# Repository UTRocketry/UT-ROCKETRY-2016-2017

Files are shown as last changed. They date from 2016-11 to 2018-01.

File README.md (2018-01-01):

# UT Rocketry Active Control Unit #
## About ##
The Active Roll Control Unit (ARCU) is an electronics platform specially designed for the 2016-2017 NASA
University Student Launch Initiative (NASA USLI) by the University of Toledo Rocketry Club.

The ARCU accomplishes the task of controlling the roll orientation of a high powered rocket (HPR) after 
motor burnout. For the 2016-2017 USLI, NASA sets the requirement that the HPR must complete 2 rolls either
CW or CCW post motor burnout and hold the final roll orientation for the remainder of the flight. This is 
accomplished through the use of a servo motor that will control the angle of fins. The ARCU is composed of 
numerous components but most notably: ATmega32u4 microcontroller (MCU) now using the ESP8266 12E module, 
MPU9250 inertial measurement unit (IMU), and a micro SD card.

The ARCU is Arduino compatable and initially used the Sparkfun Pro Micro 3.3V 8MHz bootloader. Currently the 
system uses the ESP8266 ESP12E module. The MPU9250 is a magnetometer, accelerometer, and gyroscope chip that 
will be used for position feedback in the control loop. The library for the MPU9250 is available from Sparkfun. 
Gyro and Accelerometer data is used during the flight of the rocket to control the rocket. All data from the IMU
is logged during flight and magnetometer data is analyzed post flight to verify the roll of the rocket.

The final form of the ARCU is implemented as a custom printed circuit board (PCB). However since the ARCU 
uses parts available from Sparkfun, the ARCU can be assembled easily from off the shelf components either 
on a breadboard or using protyping board.Released versions of the ARCU PCB, ARCU ICSP tool, and the Backup
Breakout version are available in the "RELEASE" sub folder.

The University of Toledo Rocketry Club learned most of the information appparent in the design and construction 
of the ARCU through the internet. If it wasn't for websites like Adafruit or Sparkfun, the ARCU project would 
not be able to be completed. Knowing this, the University of Toledo Rocketry Club has made all designs of the 
ARCU available online for public access so that others can learn from the project. The ARCU is licensed under 
the GPL 3.0 license and is Open Source Hardware and Software.

## Revision History ##
### ATMega32U4 REV A ###
- This version had issues with USB connectivity and flashing the bootloader

### ATMega32U4 REV B ###
- This version attempted fix issues with the USB in the previous version, however the fixes were unsuccessful
- THe issues may have been due to the flashing tool that was used for the bootloader

### ESP8266 REV A ###
- This board was mostly functional with the exception of the interrupt pin on the 4 pin header being non-functional

### ICSP Tool ###

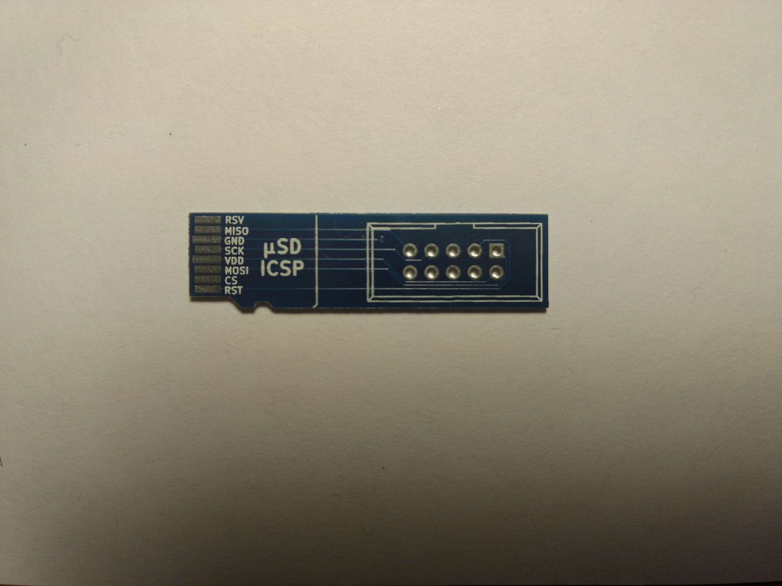
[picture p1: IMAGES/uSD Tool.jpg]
image goes here


- This was designed to flash the bootloader on the boards running the ATMega32U4. Pinouts for the ICSP header are wrong and backwards
- This tool is printed at the same thickness as a standard micro SD card and is designed to fit into a micro SD card slot.

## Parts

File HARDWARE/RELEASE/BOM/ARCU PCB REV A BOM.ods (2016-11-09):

Quantity | Reference | Value | Package | Part Number
ARCU PCB
3 | R1, R4, R5 | 10K, 5%, 1/8W | 0805 | RMCF0805JT10K0
2 | R2, R3 | 22, 5%, 1/8W | 0805 | RMCF0805JT22R0
2 | C1, C2 | 22pF, 1%, 10V | 0805 | CL21C220FBANNNC
1 | C3 | 1uF, 10%, 10V | 0805 | CL21B105KAFNNNE
3 | C4, C7, C8 | .1uF, 10%, 10V | 0805 | CL21B104KBCNNNC
1 | C5 | 10uF, 10%, 10V | 0805 | CL21A106KPFNNNE
1 | C6 | 22uF, 10%, 10V | 0805 | CL21A226MQCLQNC
1 | D1 | Schottky Diode, 1A | SOD-323 | BAT760-7
1 | D2 | Blue LED, | 0805 | LTST-C171TBKT
1 | F1 | Fuse, Poly, 500mA Hold, 1000mA Trip | 1210 | 0ZCH0050FF2G
1 | P1 | Female 1x3 Locking Polarized Conn. | CUSTOM | 5-103635-2
1 |  | Male Mating Conn. For P1 | NONE | 104257-2
3 |  | Pins for P1 Conn. | NONE | 104479-8
1 | P2 | MICRO SD, Push Push | CUSTOM | DM3CS-SF
1 | U1 | ATmega32U4, RC Clock | TQFP-44 10x10mm 0.8mm Pitch | ATMEGA32U4RC-AUR
1 | U2 | AZ1117, 3.3V Fixed Regulator | SOT-223 | AZ1117CH-3.3TRG1
1 | U3 | MPU-9250, 9 Axis IMU, I2C | QFN-40 3mmX3mm Pitch .4mm | MPU-9250
1 | U4 | ESP-01v090, Serial Wifi Module | CUSTOM | WRL-13678
1 | X1 | SMD USB OTG, Female Mini USB | CUSTOM | UX60-MB-5ST
1 | Y1 | Crystal, 8MHz | CUSTOM | ABM3-8.000MHZ-D2Y-T
University of Toledo Rocketry Club
 |  | Active Roll Control Unit (ARCU) | Rev. A 11/3/2016
Quantity | Reference | Value | Package | Part Number
ARCU ICSP
1 | P1 | 2x5 IDC Conn. | 2X5 ICSP Conn., .1” Pitch PTH | 3020-10-0100-00
Battery and Servo Wiring
1 | NONE | XT60 Conn. Male and Female Pair | NONE | PRT-10474
1 | NONE | 9V Battery Snap | NONE | Keystone 84-4
Backup Breakout Version
1 | P1 | 1X3. 1” Pitch Male Header PTH | NONE | PRT-00553
1 | U1 | Sparkfun Pro Micro 3.3V 8MHz | NONE | DEV-12587
1 | U2 | Sparkfun MPU9250 | NONE | SEN-13762
1 | U3 | Sparkfun Transflash | NONE | BOB-00544
1 | NONE | XT60 Male and Female Pair | NONE | PRT-10474
1 | NONE | 9V Battery Snap | NONE | PRT-00091
University of Toledo Rocketry Club
 |  | Active Roll Control Unit (ARCU) | Rev. A 11/3/2016

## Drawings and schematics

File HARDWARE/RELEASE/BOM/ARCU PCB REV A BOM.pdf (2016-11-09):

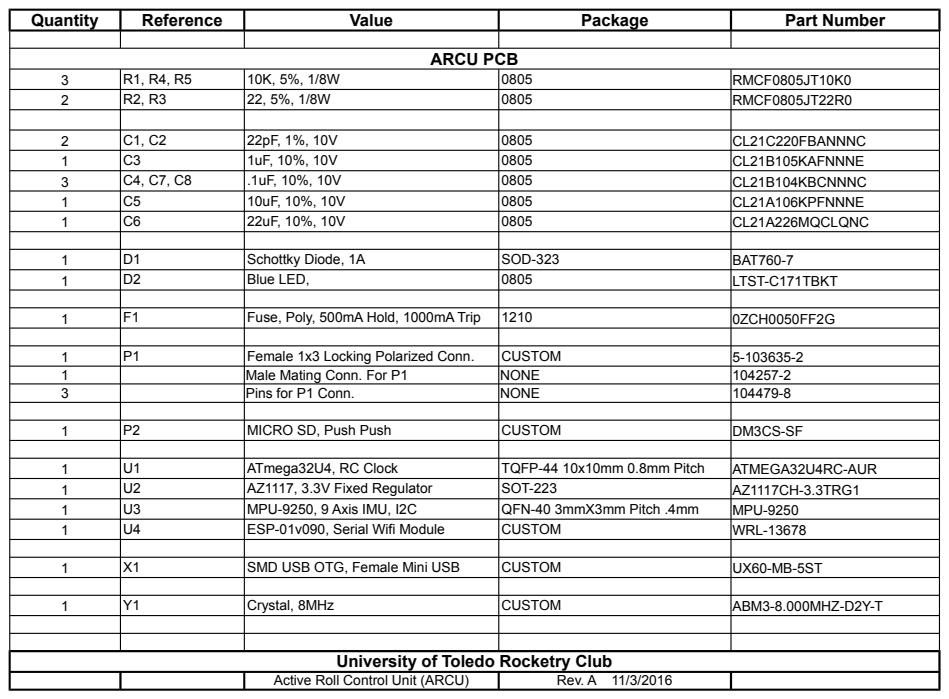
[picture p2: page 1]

University of Toledo Rocketry Club

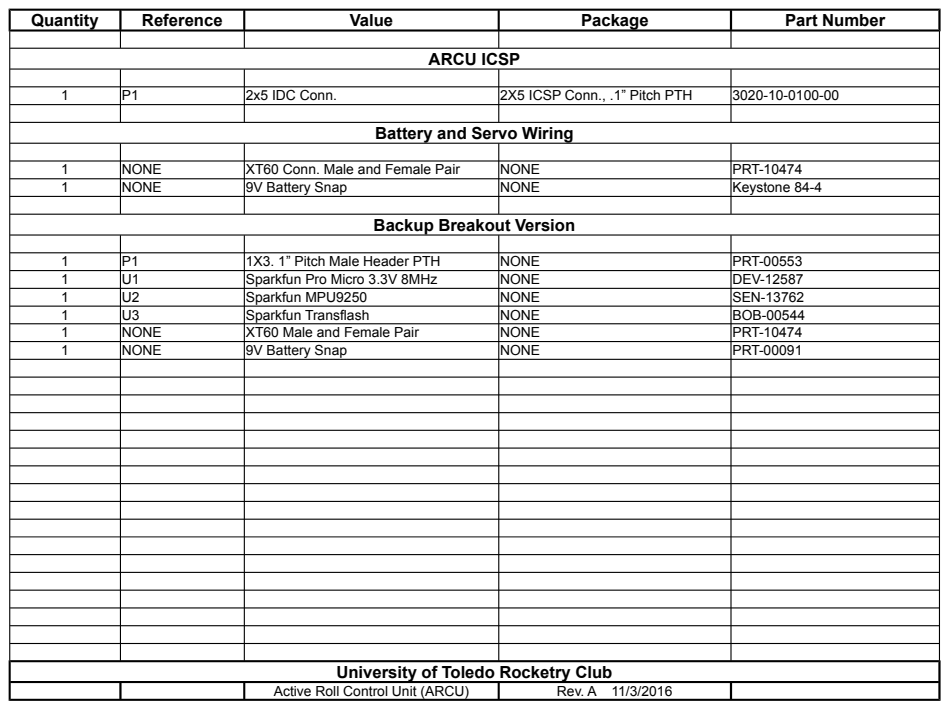
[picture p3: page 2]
Quantity; Reference; Value; Package; Part Number; ARCU ICSP; 2x5 IDC Conn.; 2X5 ICSP Conn., .1” Pitch PTH; NONE; XT60 Conn. Male and Female Pair; PRT-10474; 9V Battery Snap; Keystone 84-4; 1X3. 1” Pitch Male Header PTH; PRT-00553; Sparkfun Pro Micro 3.3V 8MHz; DEV-12587; Sparkfun MPU9250; SEN-13762; Sparkfun Transflash; BOB-00544; XT60 Male and Female Pair; PRT-00091; Active Roll Control Unit (ARCU); Rev. A 11/3/2016

Battery and Servo Wiring

Backup Breakout Version

University of Toledo Rocketry Club

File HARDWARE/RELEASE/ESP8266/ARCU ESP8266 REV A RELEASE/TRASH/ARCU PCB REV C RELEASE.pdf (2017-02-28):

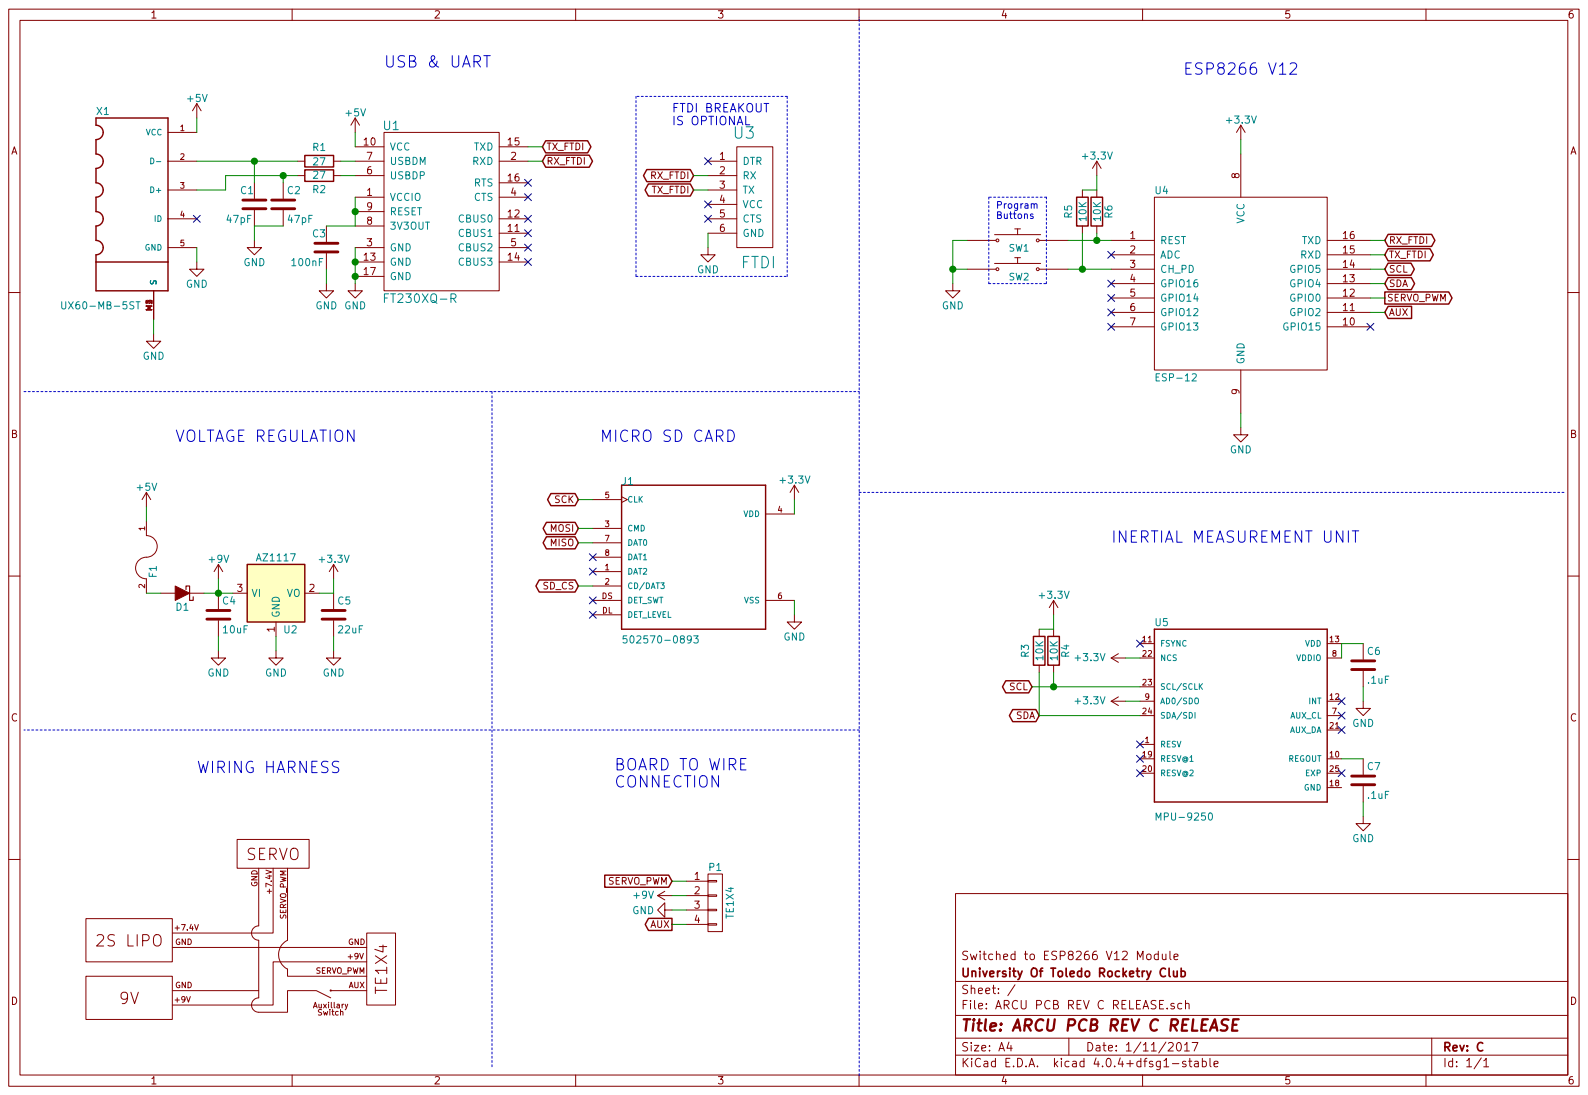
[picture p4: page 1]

+3.3V GND MICRO SD CARD

File: ARCU PCB REV C RELEASE.sch Sheet: / University Of Toledo Rocketry Club Switched to ESP8266 V12 Module

Id: 1/1 Title: ARCU PCB REV C RELEASE

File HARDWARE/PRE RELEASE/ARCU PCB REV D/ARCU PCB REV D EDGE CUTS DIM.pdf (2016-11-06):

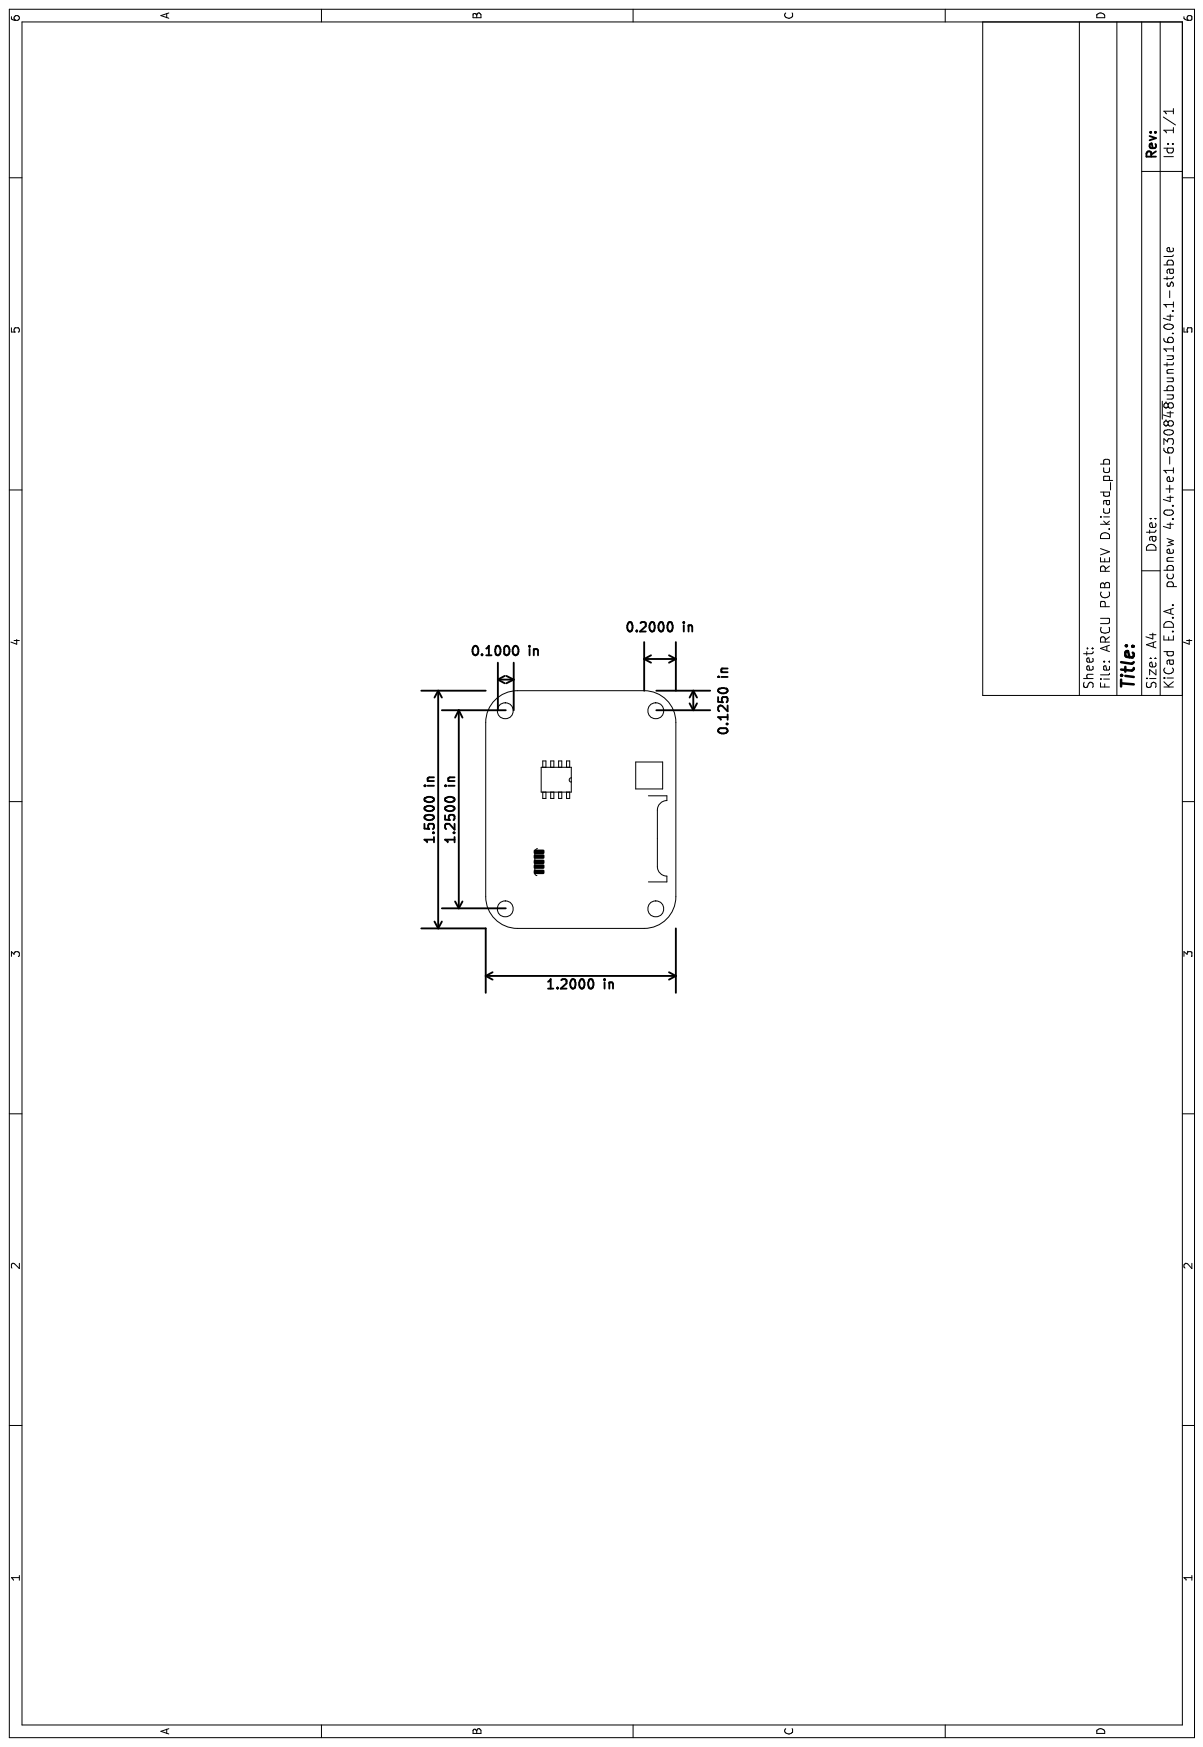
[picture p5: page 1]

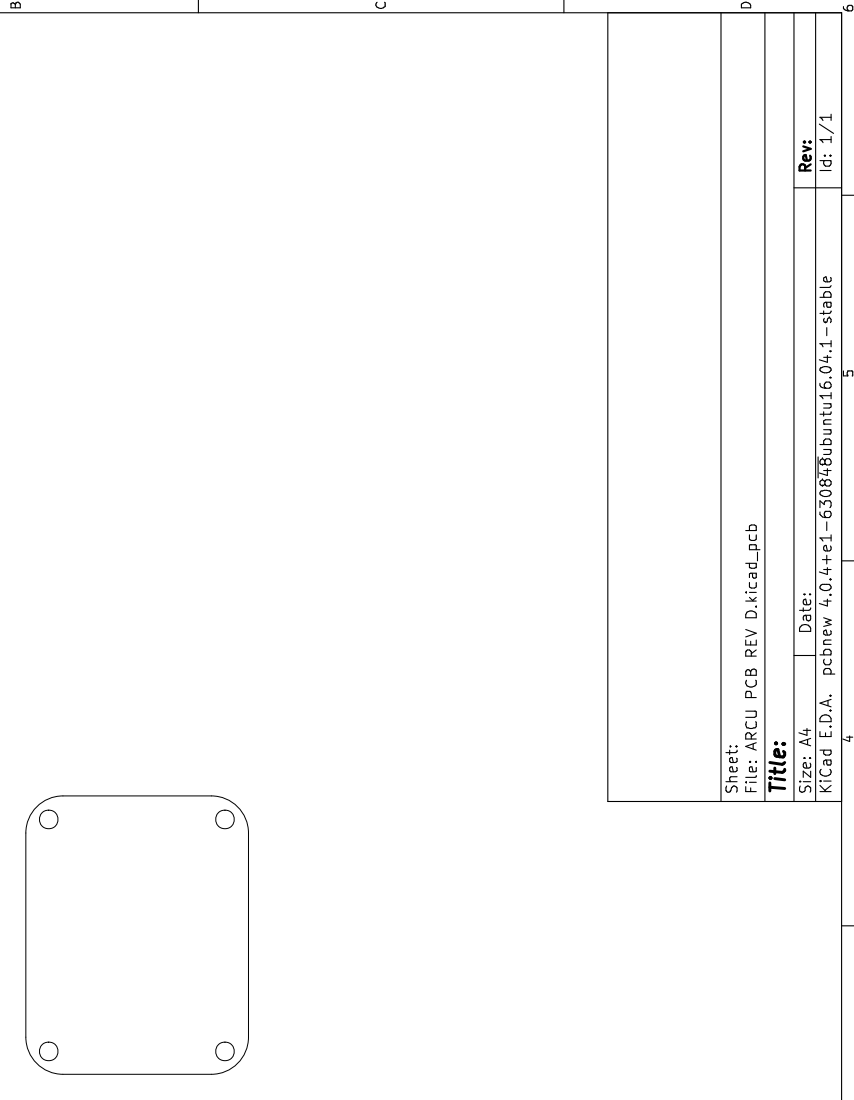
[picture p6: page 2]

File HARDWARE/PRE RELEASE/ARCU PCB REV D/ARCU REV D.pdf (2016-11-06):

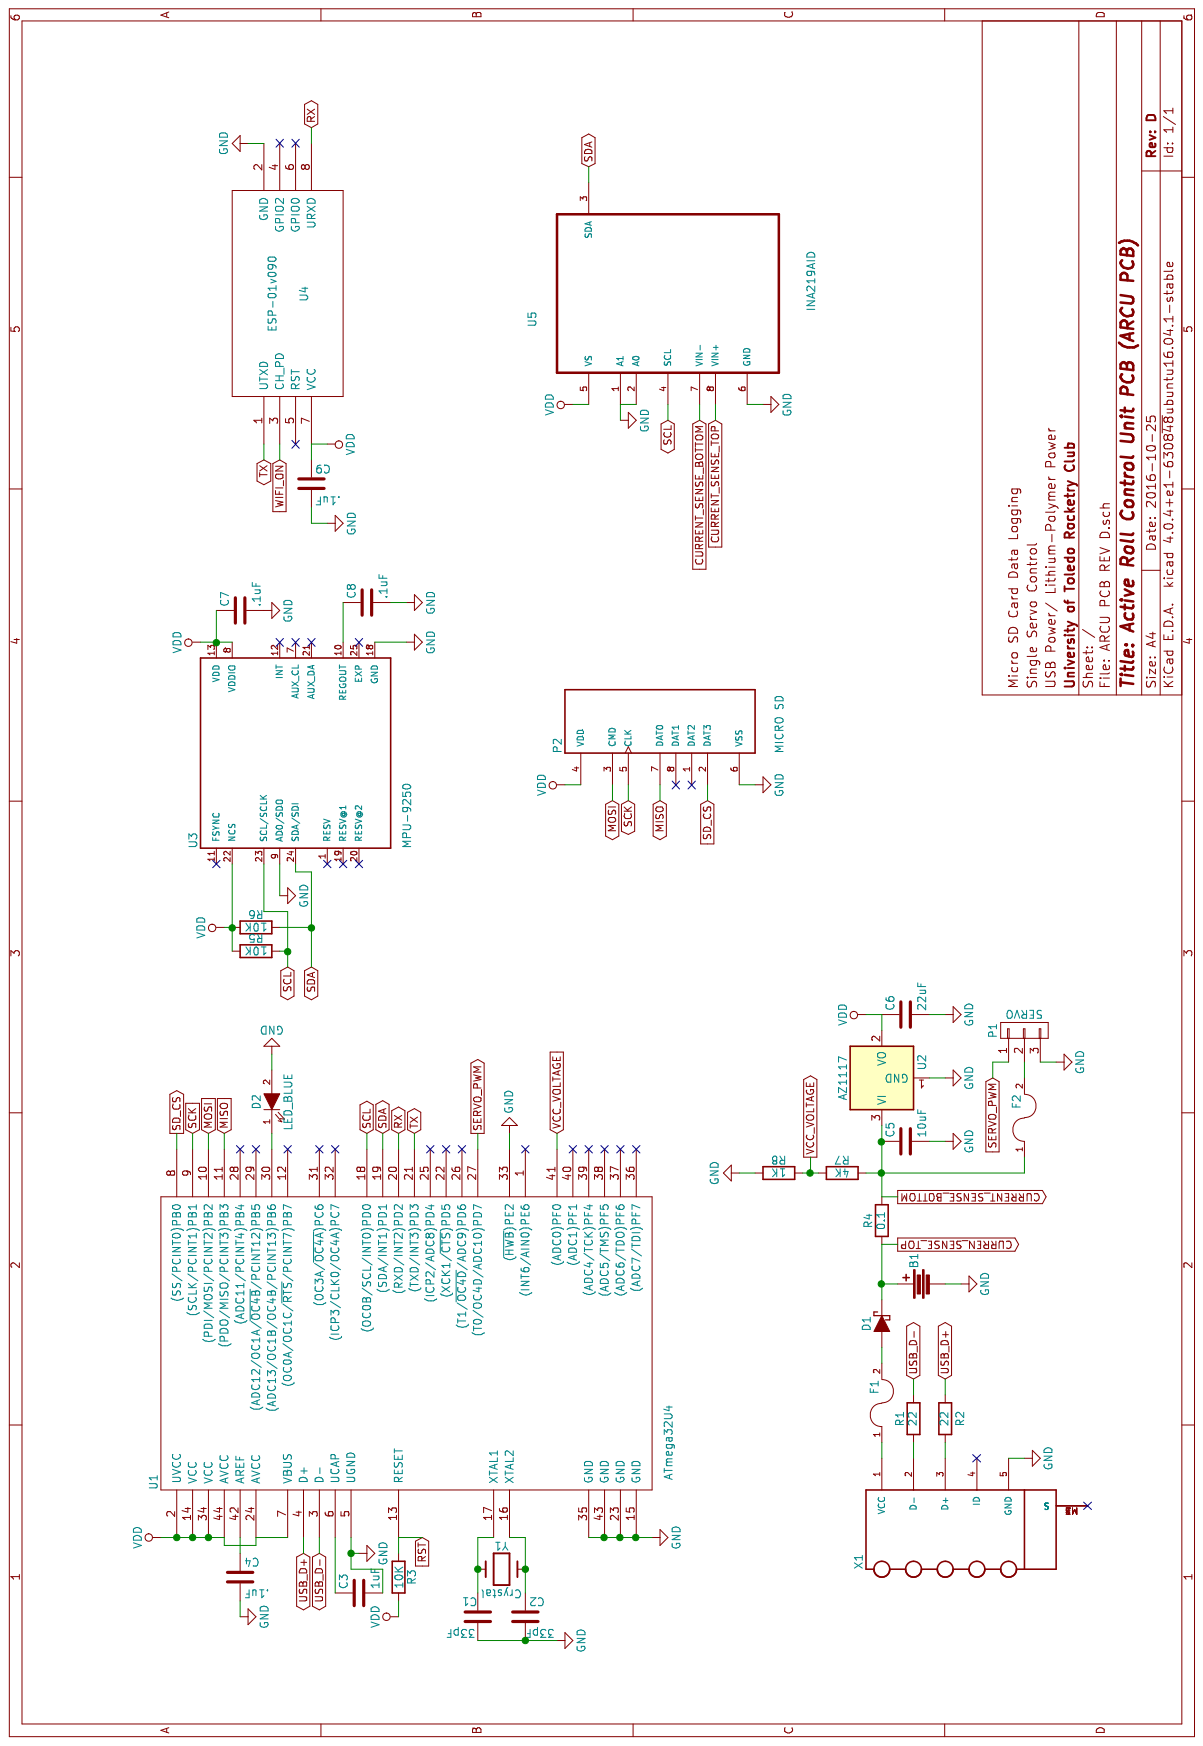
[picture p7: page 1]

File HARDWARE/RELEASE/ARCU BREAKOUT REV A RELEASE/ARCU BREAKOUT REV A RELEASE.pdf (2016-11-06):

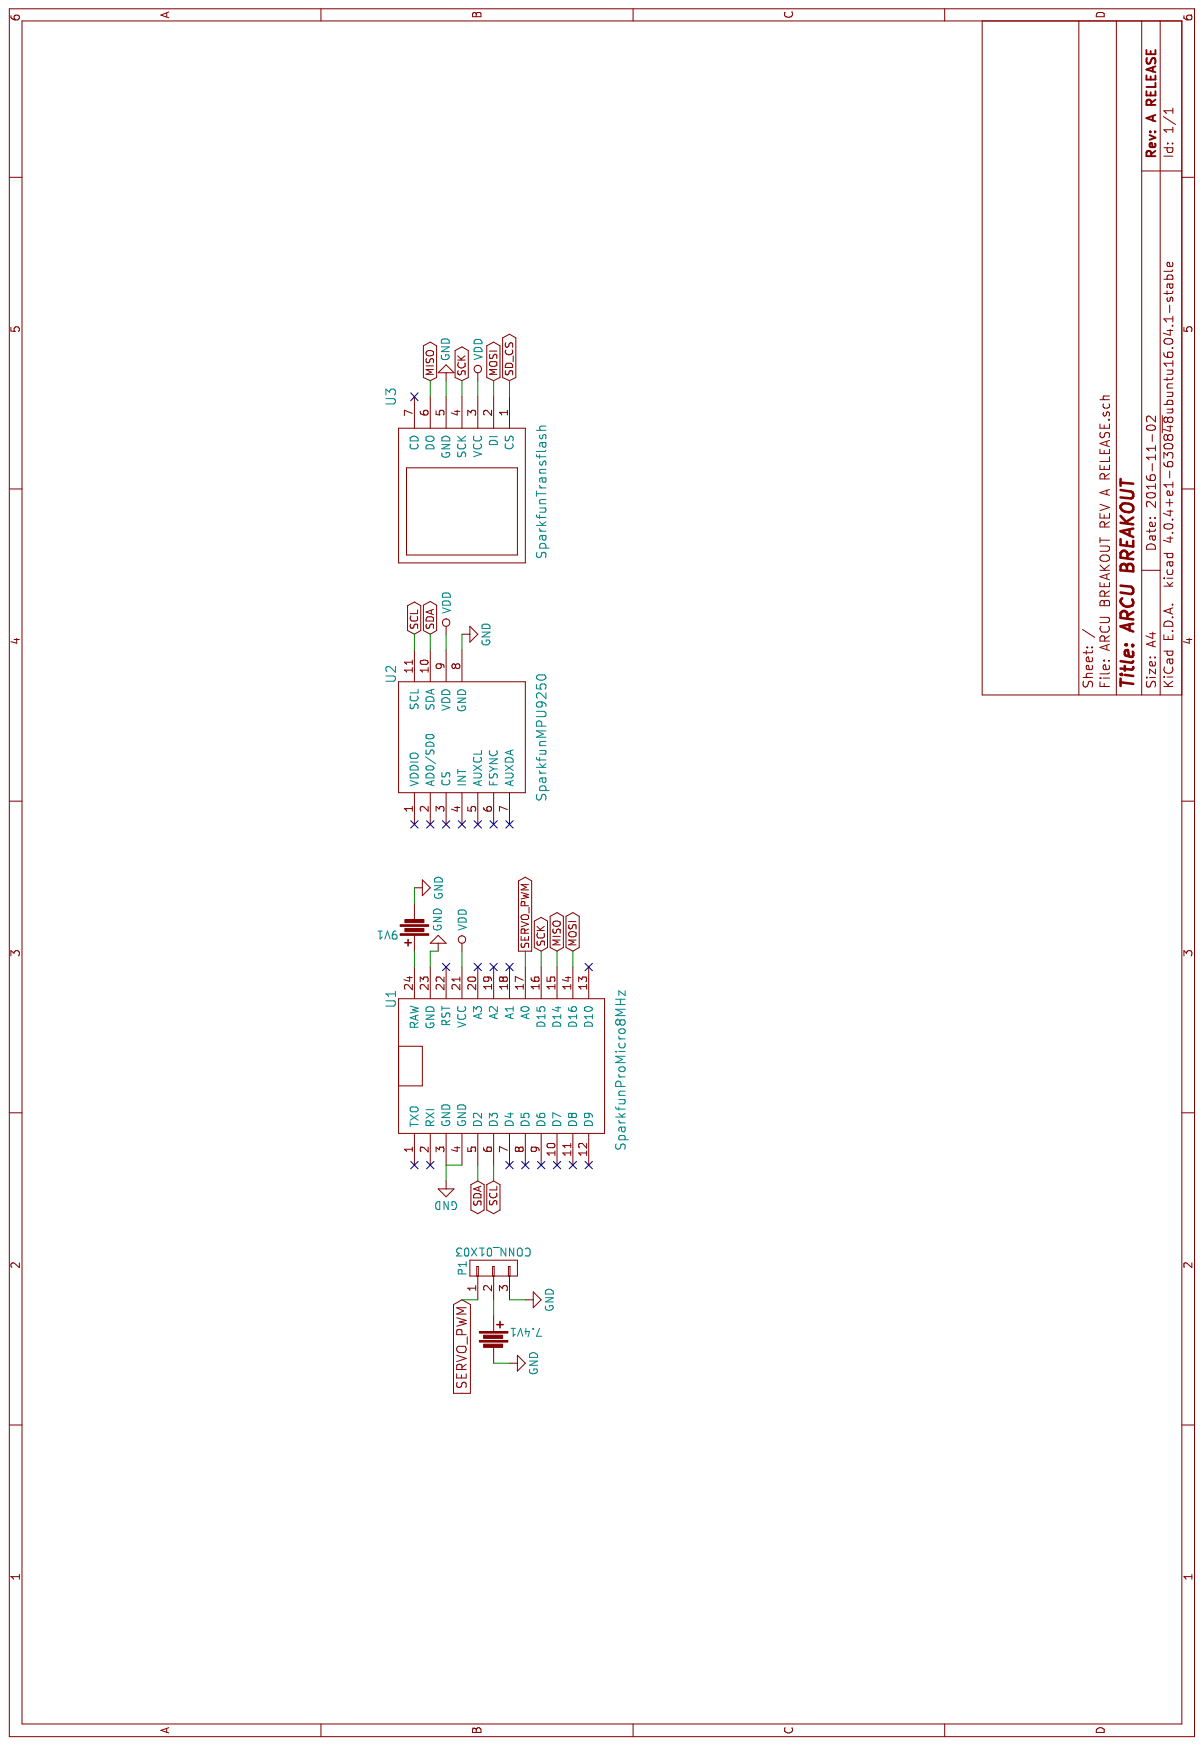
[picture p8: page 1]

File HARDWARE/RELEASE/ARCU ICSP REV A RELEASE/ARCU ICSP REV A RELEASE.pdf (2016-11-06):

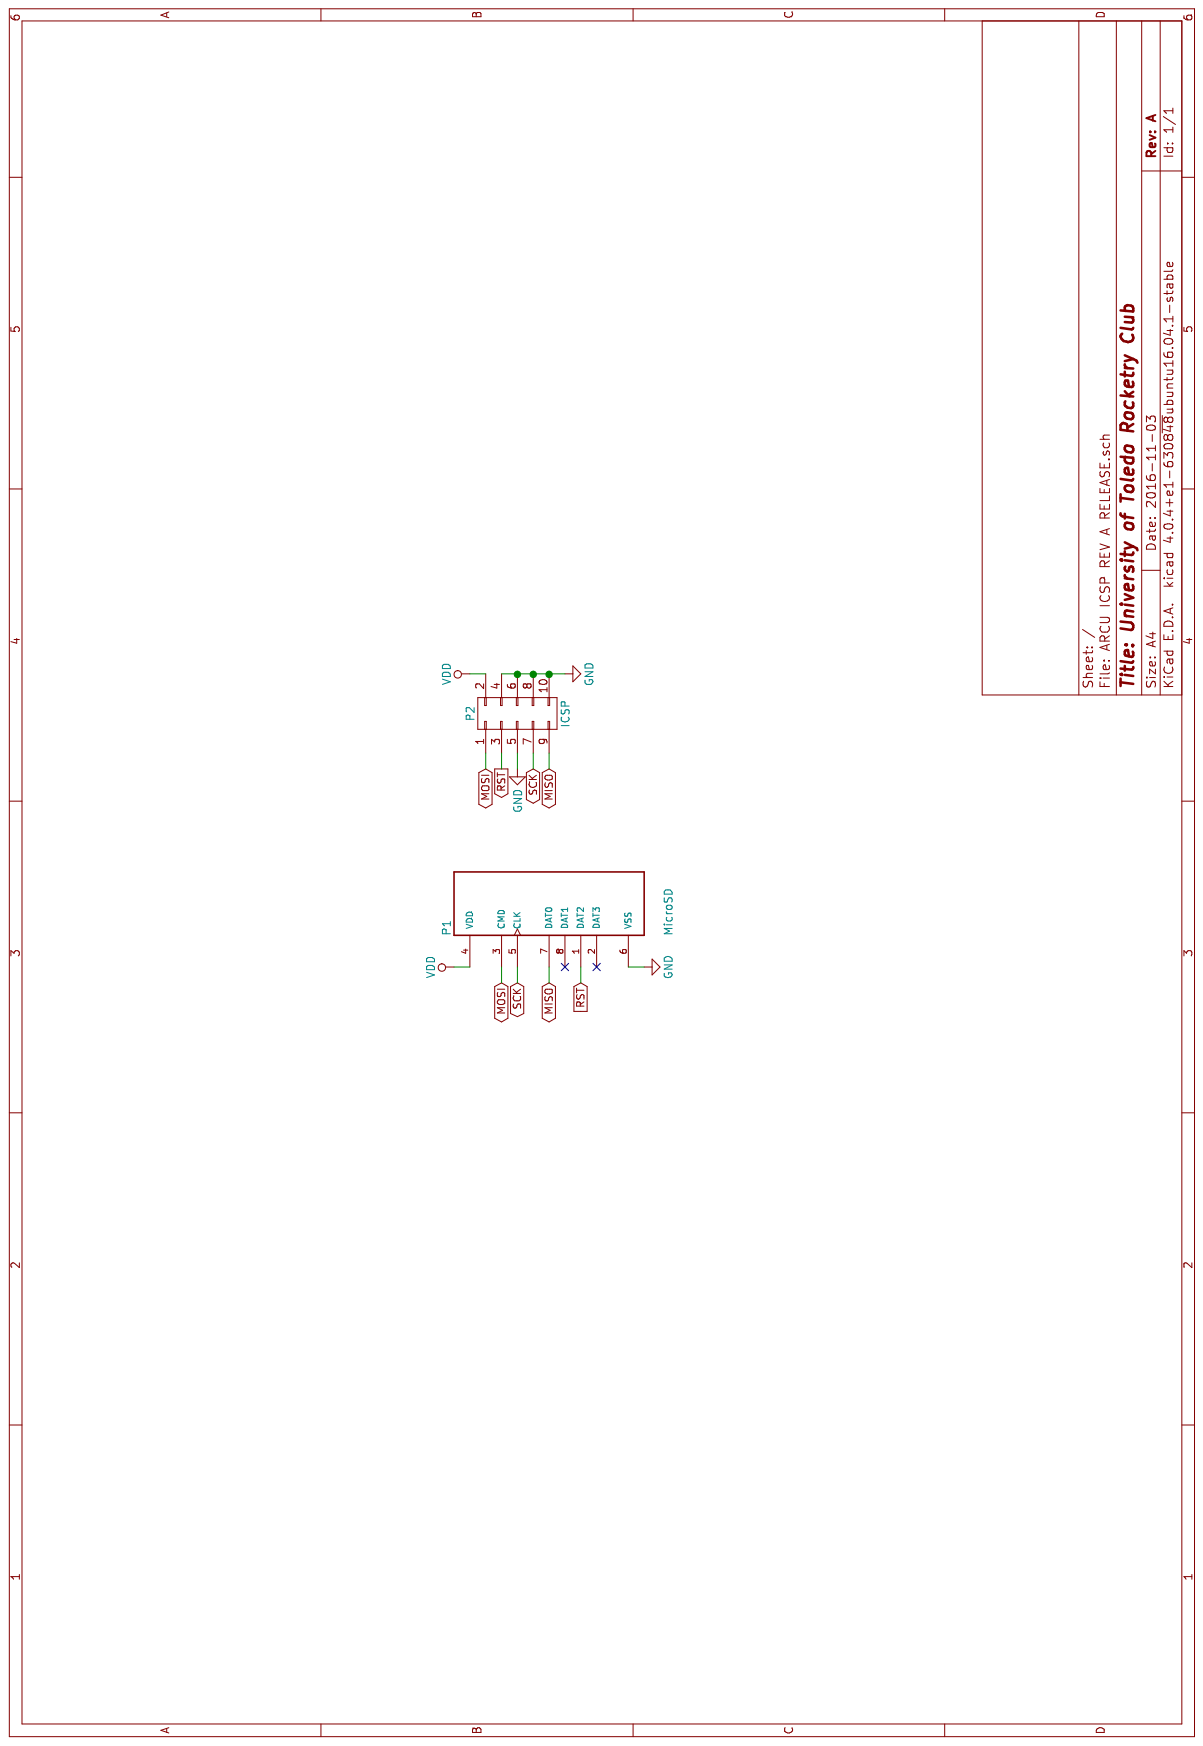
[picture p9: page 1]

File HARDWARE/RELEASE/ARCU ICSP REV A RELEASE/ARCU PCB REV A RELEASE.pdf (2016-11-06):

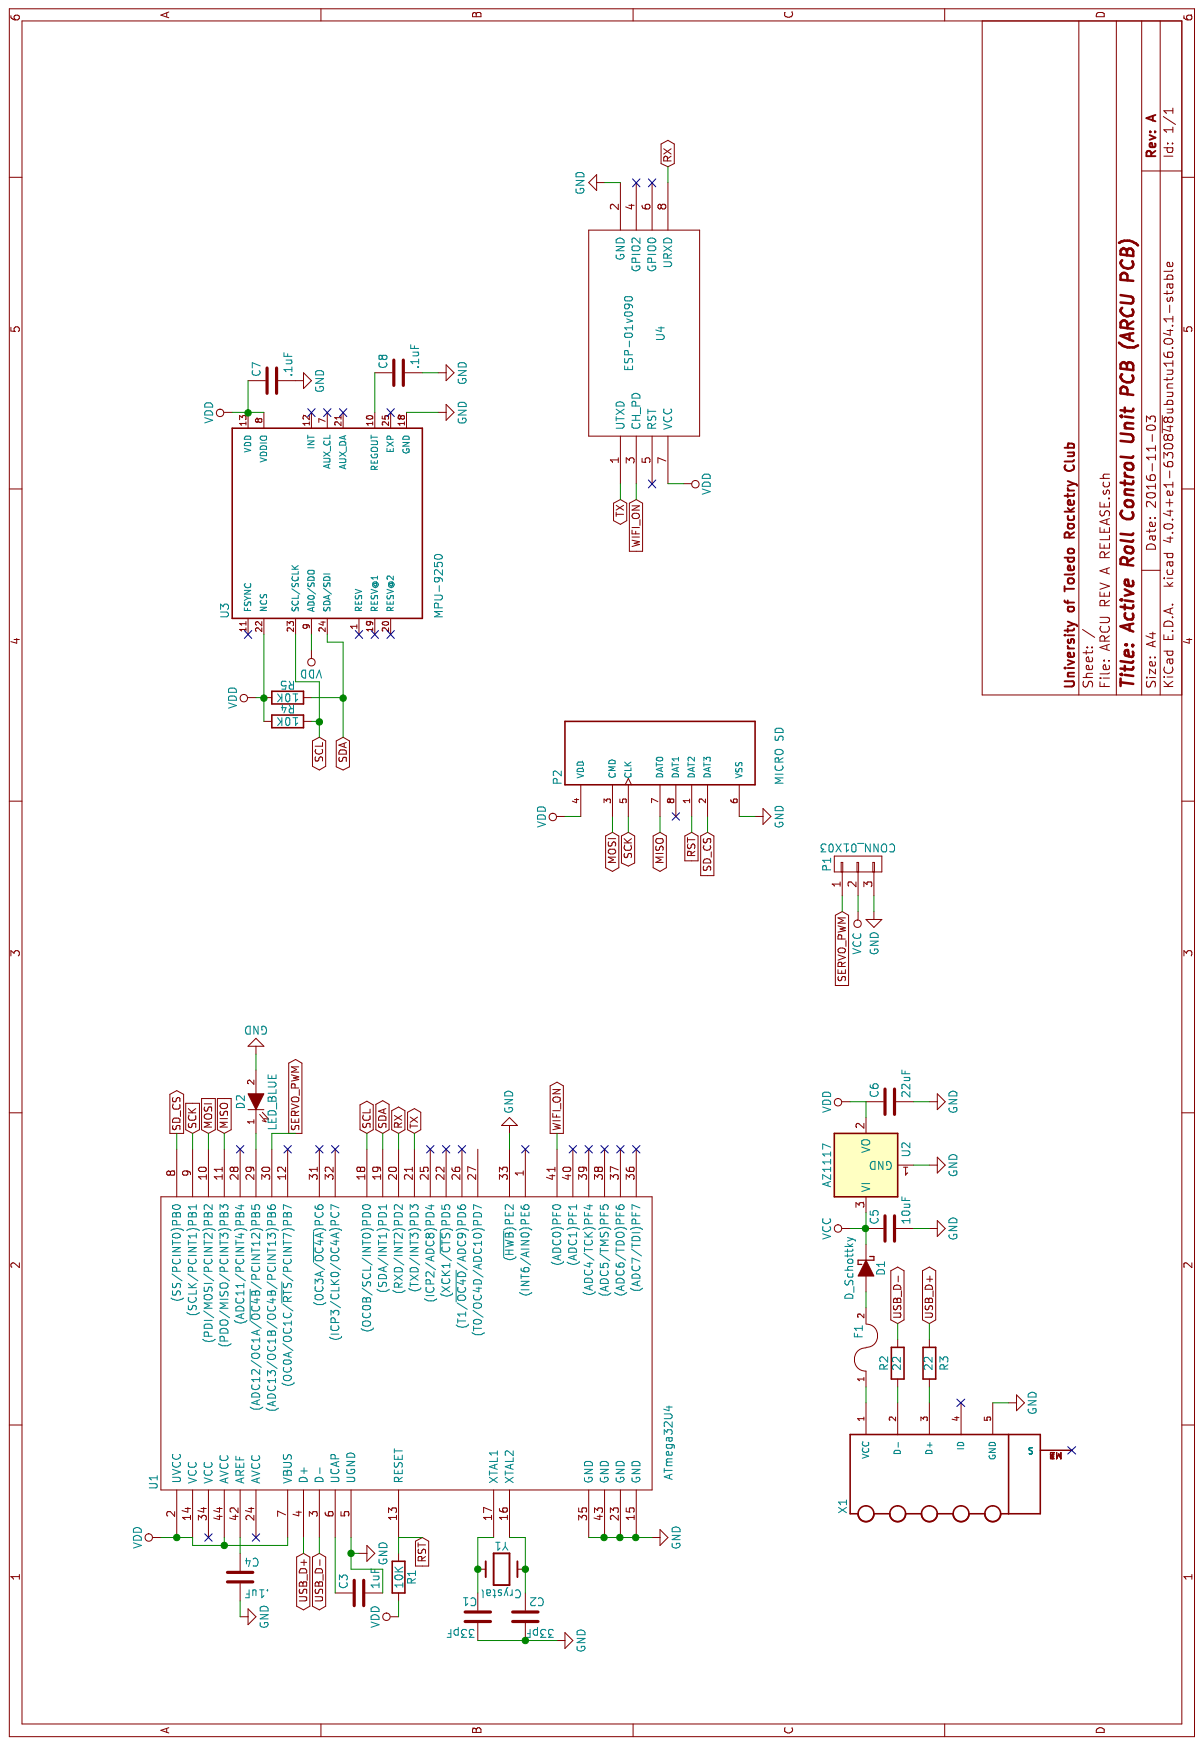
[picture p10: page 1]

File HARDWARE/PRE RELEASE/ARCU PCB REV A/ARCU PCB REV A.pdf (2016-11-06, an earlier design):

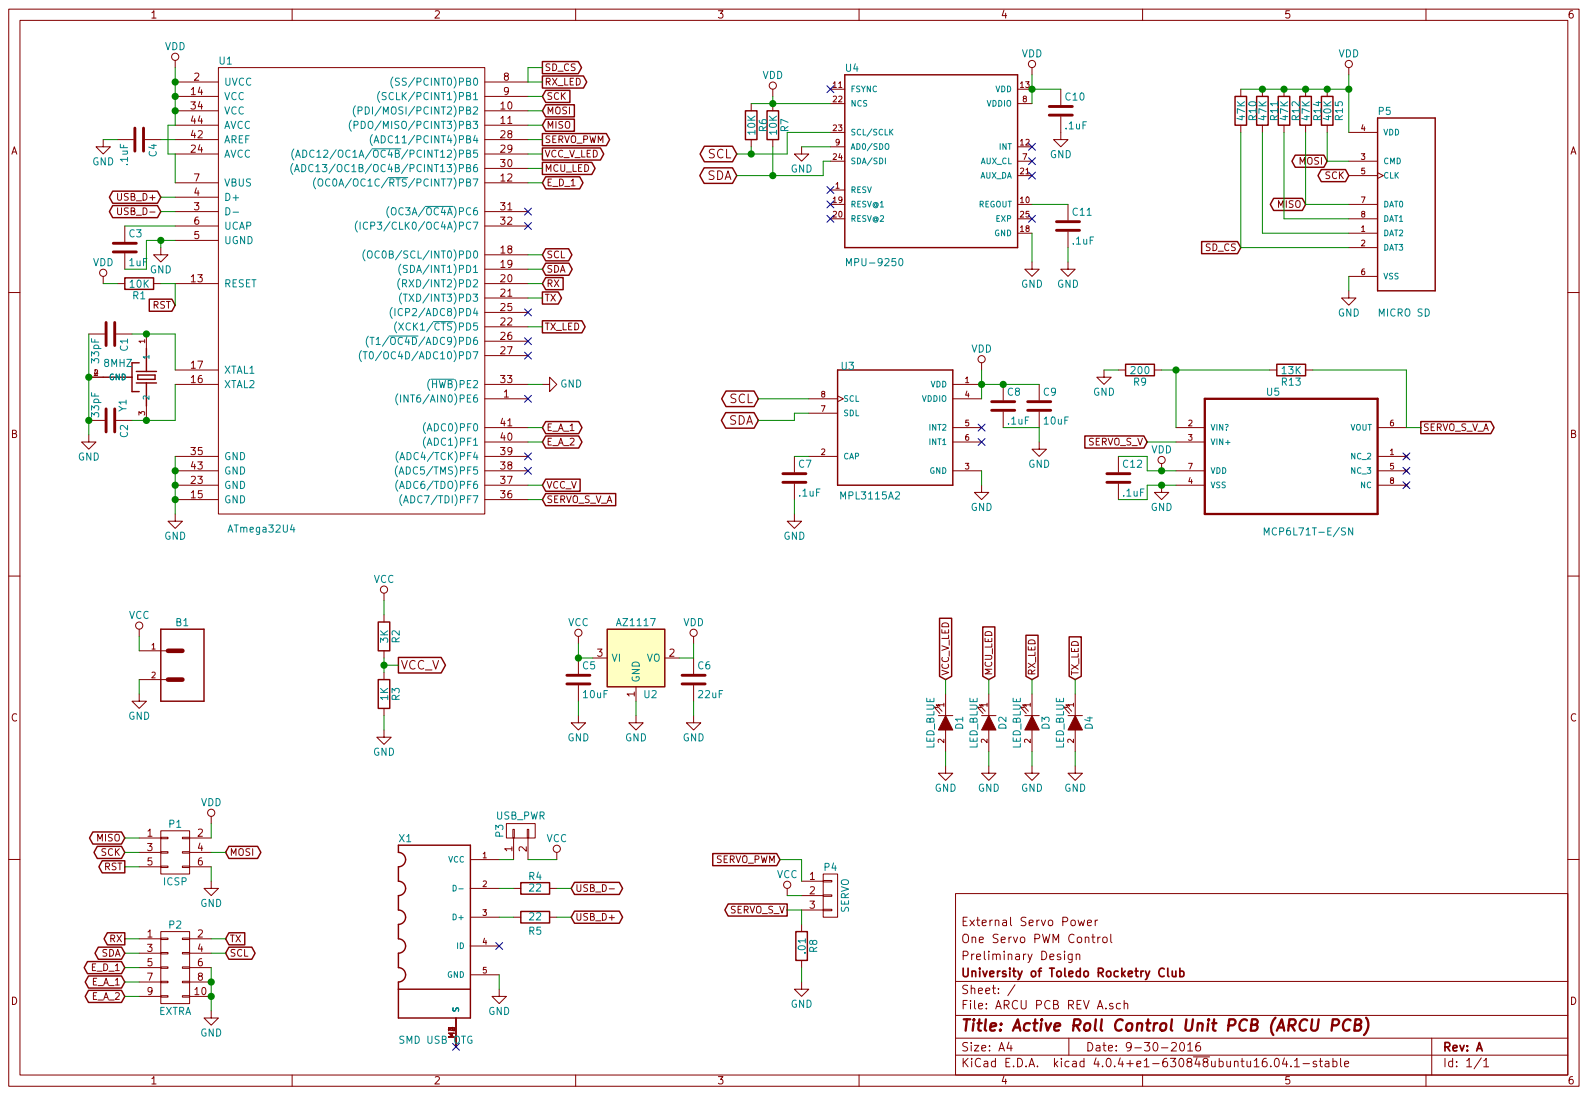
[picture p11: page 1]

1 2 D2 LED_BLUE1 2 D4 LED_BLUE RX_LED TX_LED GND GND GND GND

Preliminary Design One Servo PWM Control External Servo Power

Id: 1/1 Title: Active Roll Control Unit PCB (ARCU PCB) File: ARCU PCB REV A.sch Sheet: / University of Toledo Rocketry Club

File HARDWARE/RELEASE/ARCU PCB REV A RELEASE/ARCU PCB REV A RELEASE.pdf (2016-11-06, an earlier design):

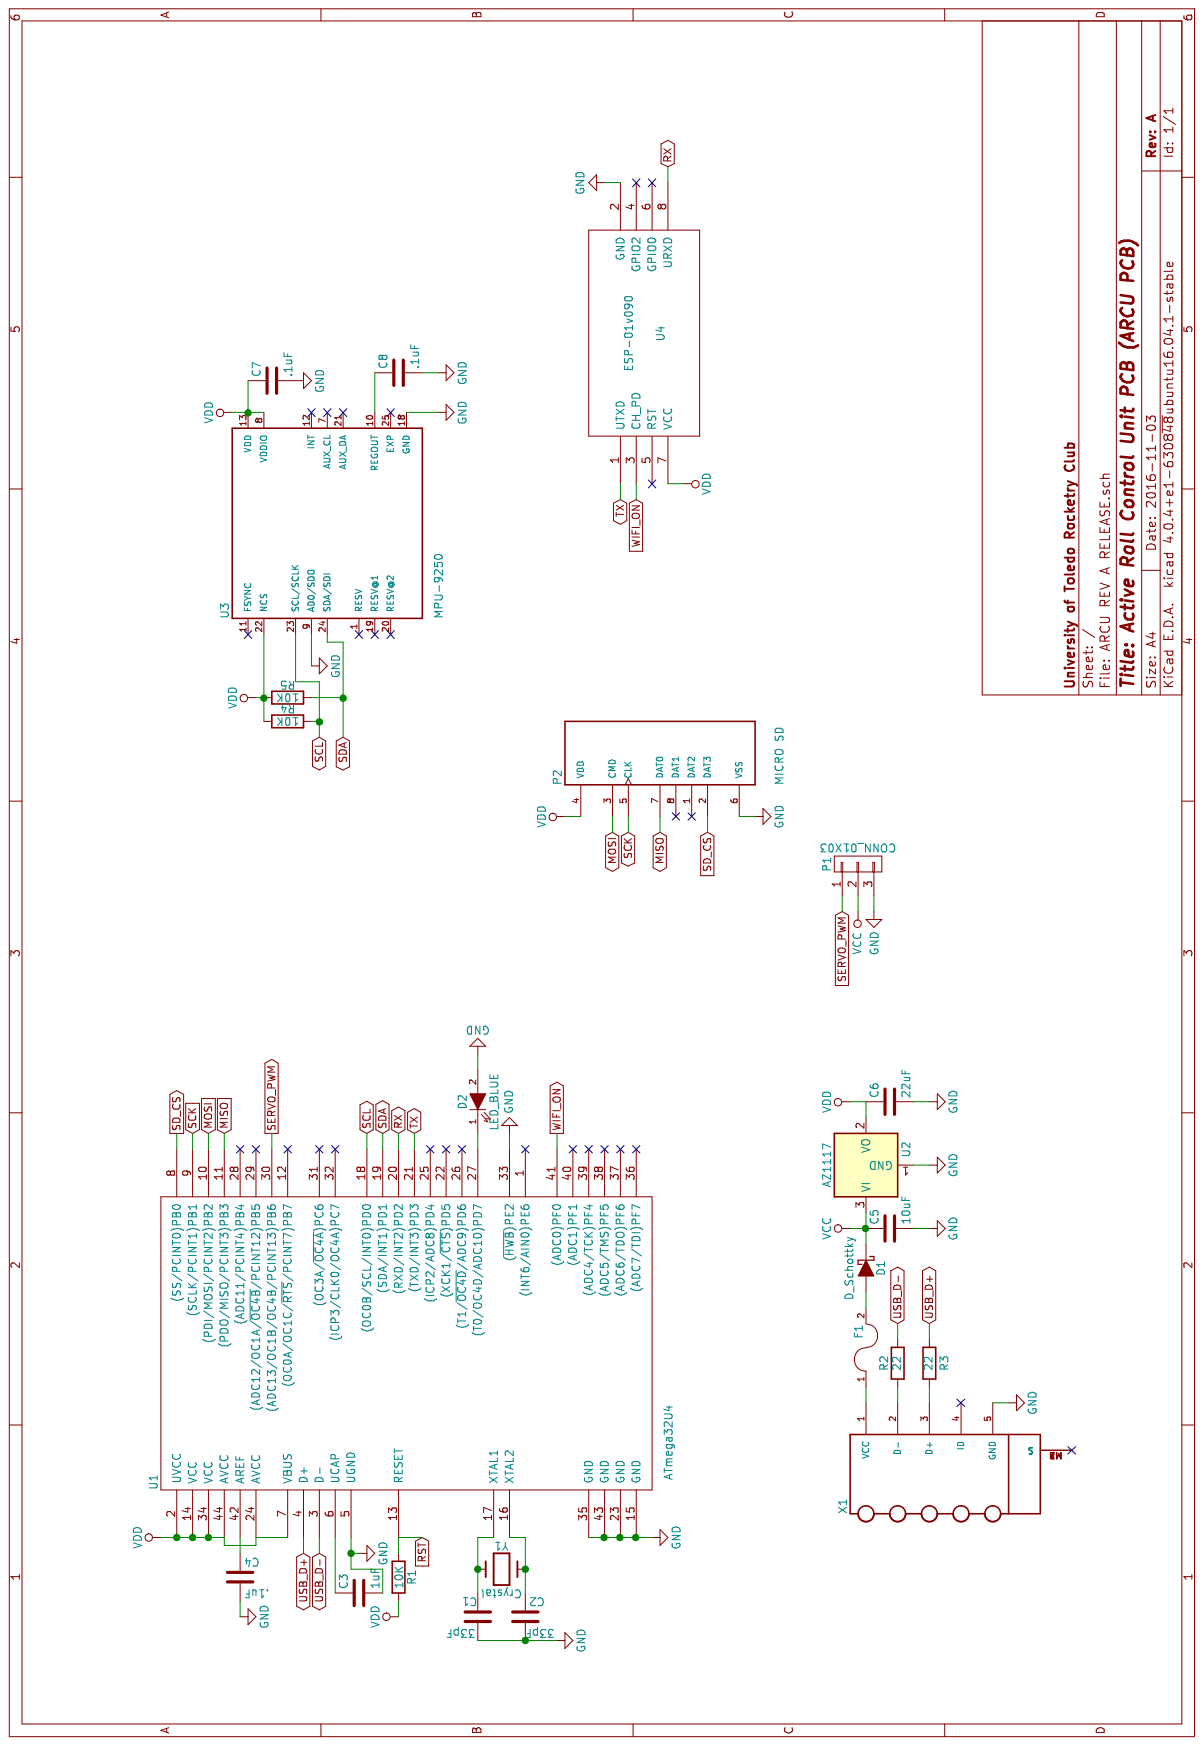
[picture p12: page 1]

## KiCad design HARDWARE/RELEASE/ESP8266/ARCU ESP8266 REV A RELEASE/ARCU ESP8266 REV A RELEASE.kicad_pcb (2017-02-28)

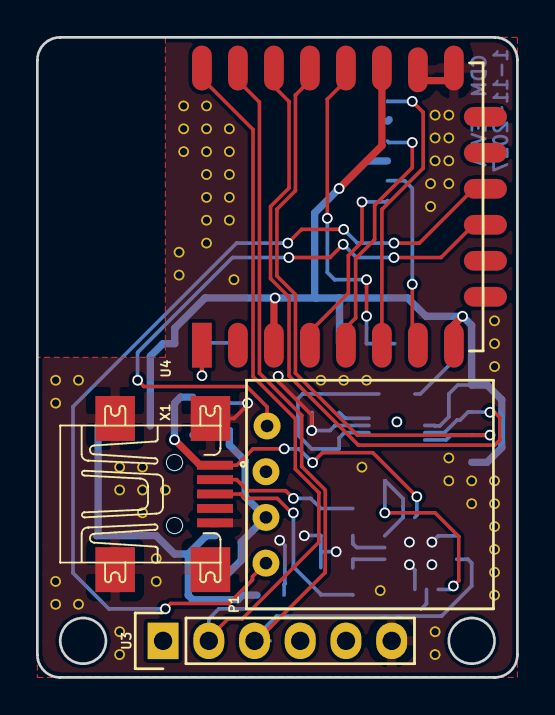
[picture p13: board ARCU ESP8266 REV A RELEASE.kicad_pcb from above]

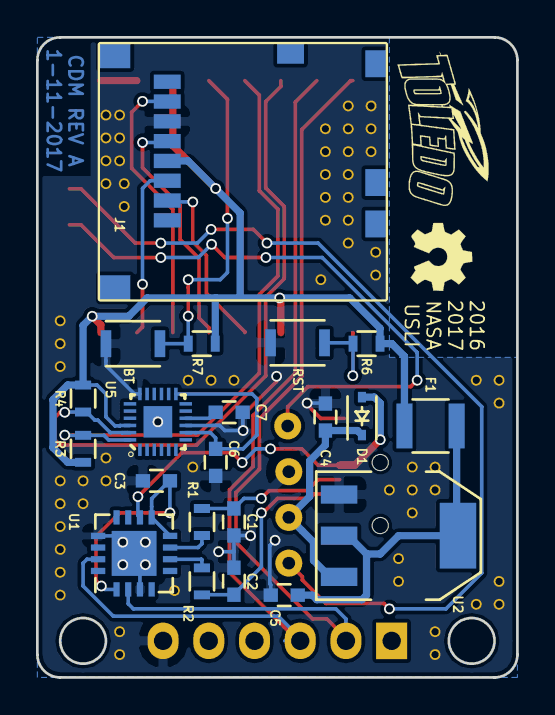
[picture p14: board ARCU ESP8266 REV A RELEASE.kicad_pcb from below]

Board: 2 copper layers, 26.7 x 35.6 mm, 25 parts (21 on the bottom side), 24 nets.

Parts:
BT: Push_SW; KXT 131 LHS
C1, C2: 47pF; C_0603
C3, C6, C7: .1uF; C_0603
C4: 10uF; C_0603
C5: 22uF; C_0603
D1: D_Schottky; SOD-323
F1: FUSE; R_1210
J1: 502570-0893; MOLEX_502570-0893
P1: TE1X4
R1, R2: 27; R_0603
R3, R4, R6, R7: 10K; R_0603
RST: Push_SW; KXT 131 LHS
U1: FT230XQ-R; QFN-16-1EP_4x4mm_Pitch0.65mm
U2: AZ1117; SOT-223
U3: FTDI; Pin_Header_Straight_1x06
U4: ESP-12E
U5: MPU-9250; QFN40P300X300X105-25N
X1: UX60-MB-5ST

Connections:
+3V3: F1.1, J1.4, R3.1, R4.1, R6.1, R7.1, U4.3, U4.8, U4.17, U5.22
+5V: D1.2, U1.10, X1.1
+9V: C4.1, D1.1, P1.2, U2.3
AUX: P1.4, U4.11
GND: BT.1, C1.2, C2.2, C3.2, C4.2, C5.2, C6.2, C7.2, J1.6, P1.3, RST.1, U1.3, U1.13, U1.17, U2.1, U3.6, U4.15, U4.16, U5.9, U5.18, X1.5, X1.M1, X1.M2, X1.M3, X1.M4
MISO: J1.7, U4.6
MOSI: J1.3, U4.7
unnamed: BT.2, R7.2, U4.18
unnamed: C1.1, R1.2, X1.2
unnamed: C2.1, R2.1, X1.3
unnamed: C3.1, U1.1, U1.8, U1.9
unnamed: C5.1, F1.2, U2.2
unnamed: C6.1, U5.8, U5.13
unnamed: C7.1, U5.10
unnamed: R1.1, U1.7
unnamed: R2.2, U1.6
unnamed: R6.2, RST.2, U4.1
RX_FTDI: U1.2, U3.2, U4.22
SCK: J1.5, U4.5
SCL: R4.2, U4.20, U5.23
SDA: R3.2, U4.19, U5.24
SD_CS: J1.2, U4.4
SERVO_PWM: P1.1, U4.12
TX_FTDI: U1.15, U3.3, U4.21

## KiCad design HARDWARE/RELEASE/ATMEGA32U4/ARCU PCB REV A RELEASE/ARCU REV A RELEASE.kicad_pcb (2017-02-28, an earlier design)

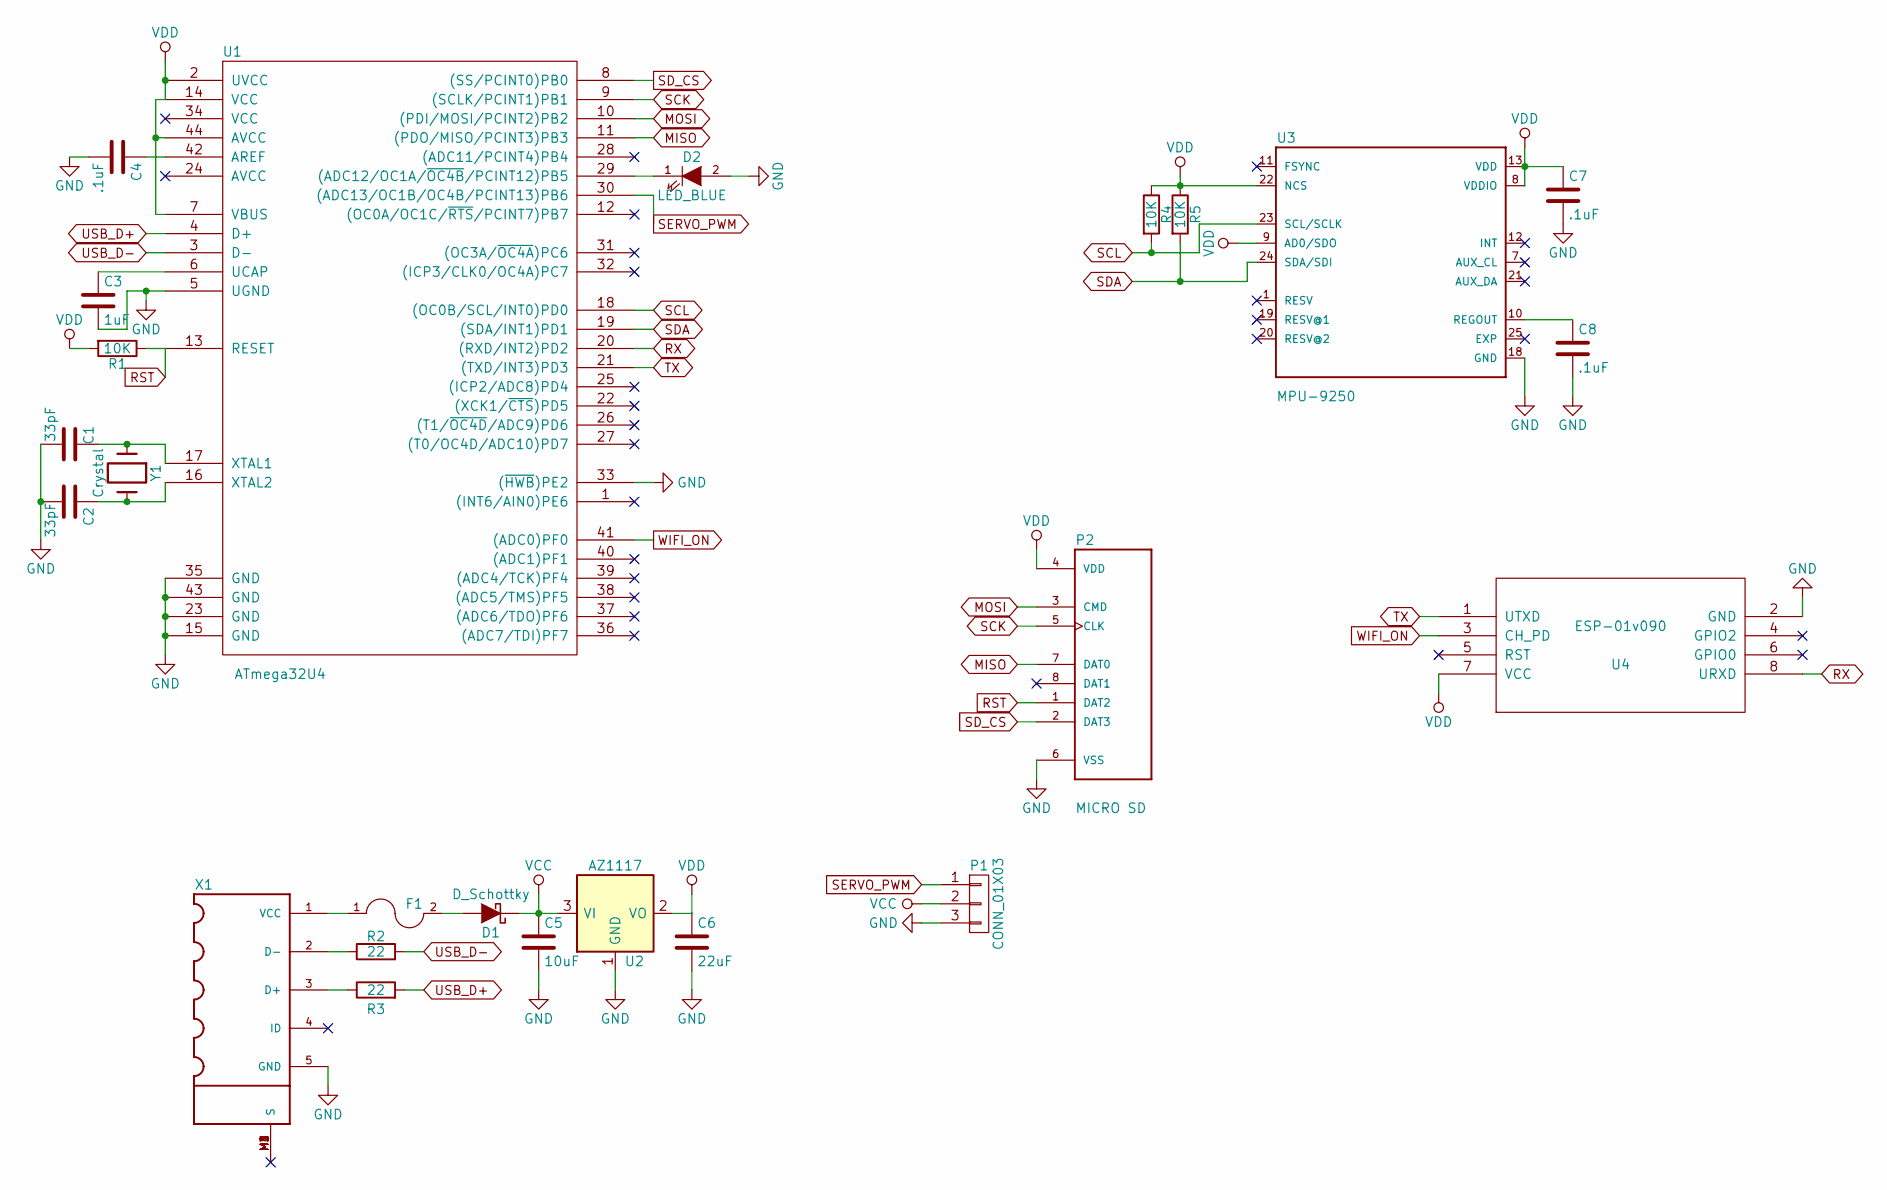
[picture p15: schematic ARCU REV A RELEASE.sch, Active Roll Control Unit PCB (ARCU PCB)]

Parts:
C1, C2: 33pF; C_0805
C3: 1uF; C_0805
C4, C7, C8: .1uF; C_0805
C5: 10uF; C_0805
C6: 22uF; C_0805
D1: D_Schottky; SOD-323
D2: LED_BLUE; LED_0805
F1: FUSE; R_1210
P1: CONN_01X03; TE1X3
P2: MICRO SD; HRS_DM3CS-SF
R1, R4, R5: 10K; R_0805
R2, R3: 22; R_0805
U1: ATmega32U4; TQFP-44_10x10mm_Pitch0.8mm
U2: AZ1117; SOT-223
U3: MPU-9250; QFN40P300X300X105-25N
U4: ESP-01v090; ESP-01
X1: SMD USB OTG; UX60-MB-5ST
Y1: Crystal; ABM3

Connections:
GND: C1.2, C2.2, C3.2, C4.2, C5.2, C6.2, C7.2, C8.2, D2.2 (A), P1.3, P2.6 (VSS), U1.5 (UGND), U1.15 (GND), U1.23 (GND), U1.33 ((~HWB~)PE2), U1.35 (GND), U1.43 (GND), U2.1 (GND), U3.18 (GND), U4.2 (GND), X1.5 (GND)
MISO: P2.7 (DAT0), U1.11 ((PDO/MISO/PCINT3)PB3)
MOSI: P2.3 (CMD), U1.10 ((PDI/MOSI/PCINT2)PB2)
unnamed: C1.1, U1.17 (XTAL1), Y1.1
unnamed: C2.1, U1.16 (XTAL2), Y1.2
unnamed: C3.1, U1.6 (UCAP)
unnamed: C4.1, U1.42 (AREF)
unnamed: C8.1, U3.10 (REGOUT)
unnamed: D1.2 (A), F1.2
unnamed: D2.1 (K), U1.29 ((ADC12/OC1A/~OC4B~/PCINT12)PB5)
unnamed: F1.1, X1.1 (VCC)
unnamed: R2.1, X1.2 (D-)
unnamed: R3.1, X1.3 (D+)
RST: P2.1 (DAT2), R1.1, U1.13 (RESET)
RX: U1.20 ((RXD/INT2)PD2), U4.8 (URXD)
SCK: P2.5 (CLK), U1.9 ((SCLK/PCINT1)PB1)
SCL: R4.2, U1.18 ((OC0B/SCL/INT0)PD0), U3.23 (SCL/SCLK)
SDA: R5.2, U1.19 ((SDA/INT1)PD1), U3.24 (SDA/SDI)
SD_CS: P2.2 (DAT3), U1.8 ((SS/PCINT0)PB0)
SERVO_PWM: P1.1, U1.30 ((ADC13/OC1B/OC4B/PCINT13)PB6)
TX: U1.21 ((TXD/INT3)PD3), U4.1 (UTXD)
USB_D+: R3.2, U1.4 (D+)
USB_D-: R2.2, U1.3 (D-)
VCC: C5.1, D1.1 (K), P1.2, U2.3 (VI)
VDD: C6.1, C7.1, P2.4 (VDD), R1.2, R4.1, R5.1, U1.2 (UVCC), U1.7 (VBUS), U1.14 (VCC), U1.44 (AVCC), U2.2 (VO), U3.8 (VDDIO), U3.9 (AD0/SDO), U3.13 (VDD), U3.22 (NCS), U4.7 (VCC)
WIFI_ON: U1.41 ((ADC0)PF0), U4.3 (CH_PD)

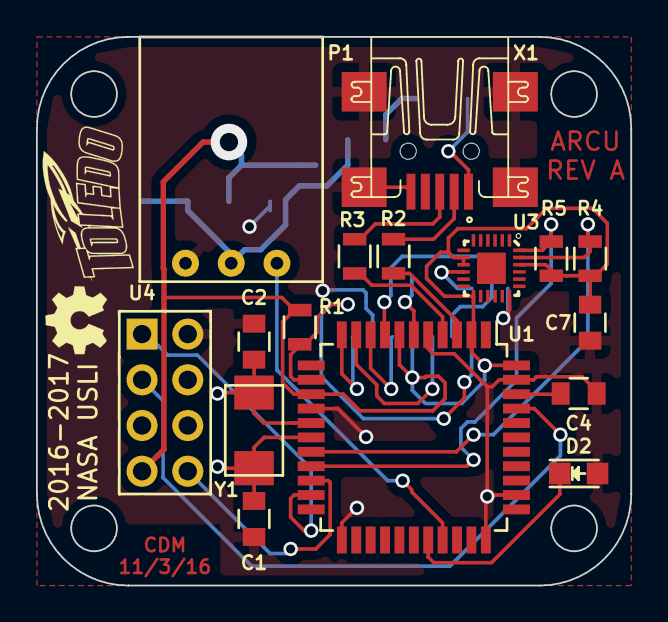
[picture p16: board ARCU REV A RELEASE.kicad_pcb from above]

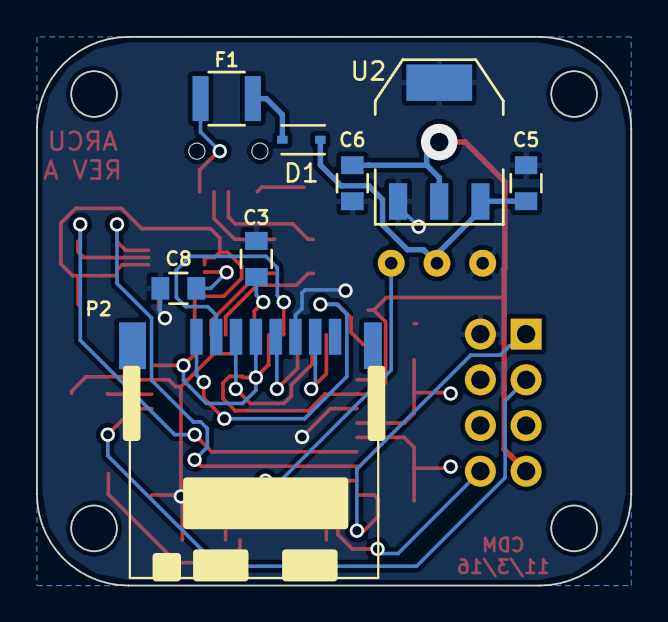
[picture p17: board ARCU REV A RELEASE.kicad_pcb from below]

Board: 2 copper layers, 33.0 x 30.5 mm, 24 parts (8 on the bottom side), 26 nets.

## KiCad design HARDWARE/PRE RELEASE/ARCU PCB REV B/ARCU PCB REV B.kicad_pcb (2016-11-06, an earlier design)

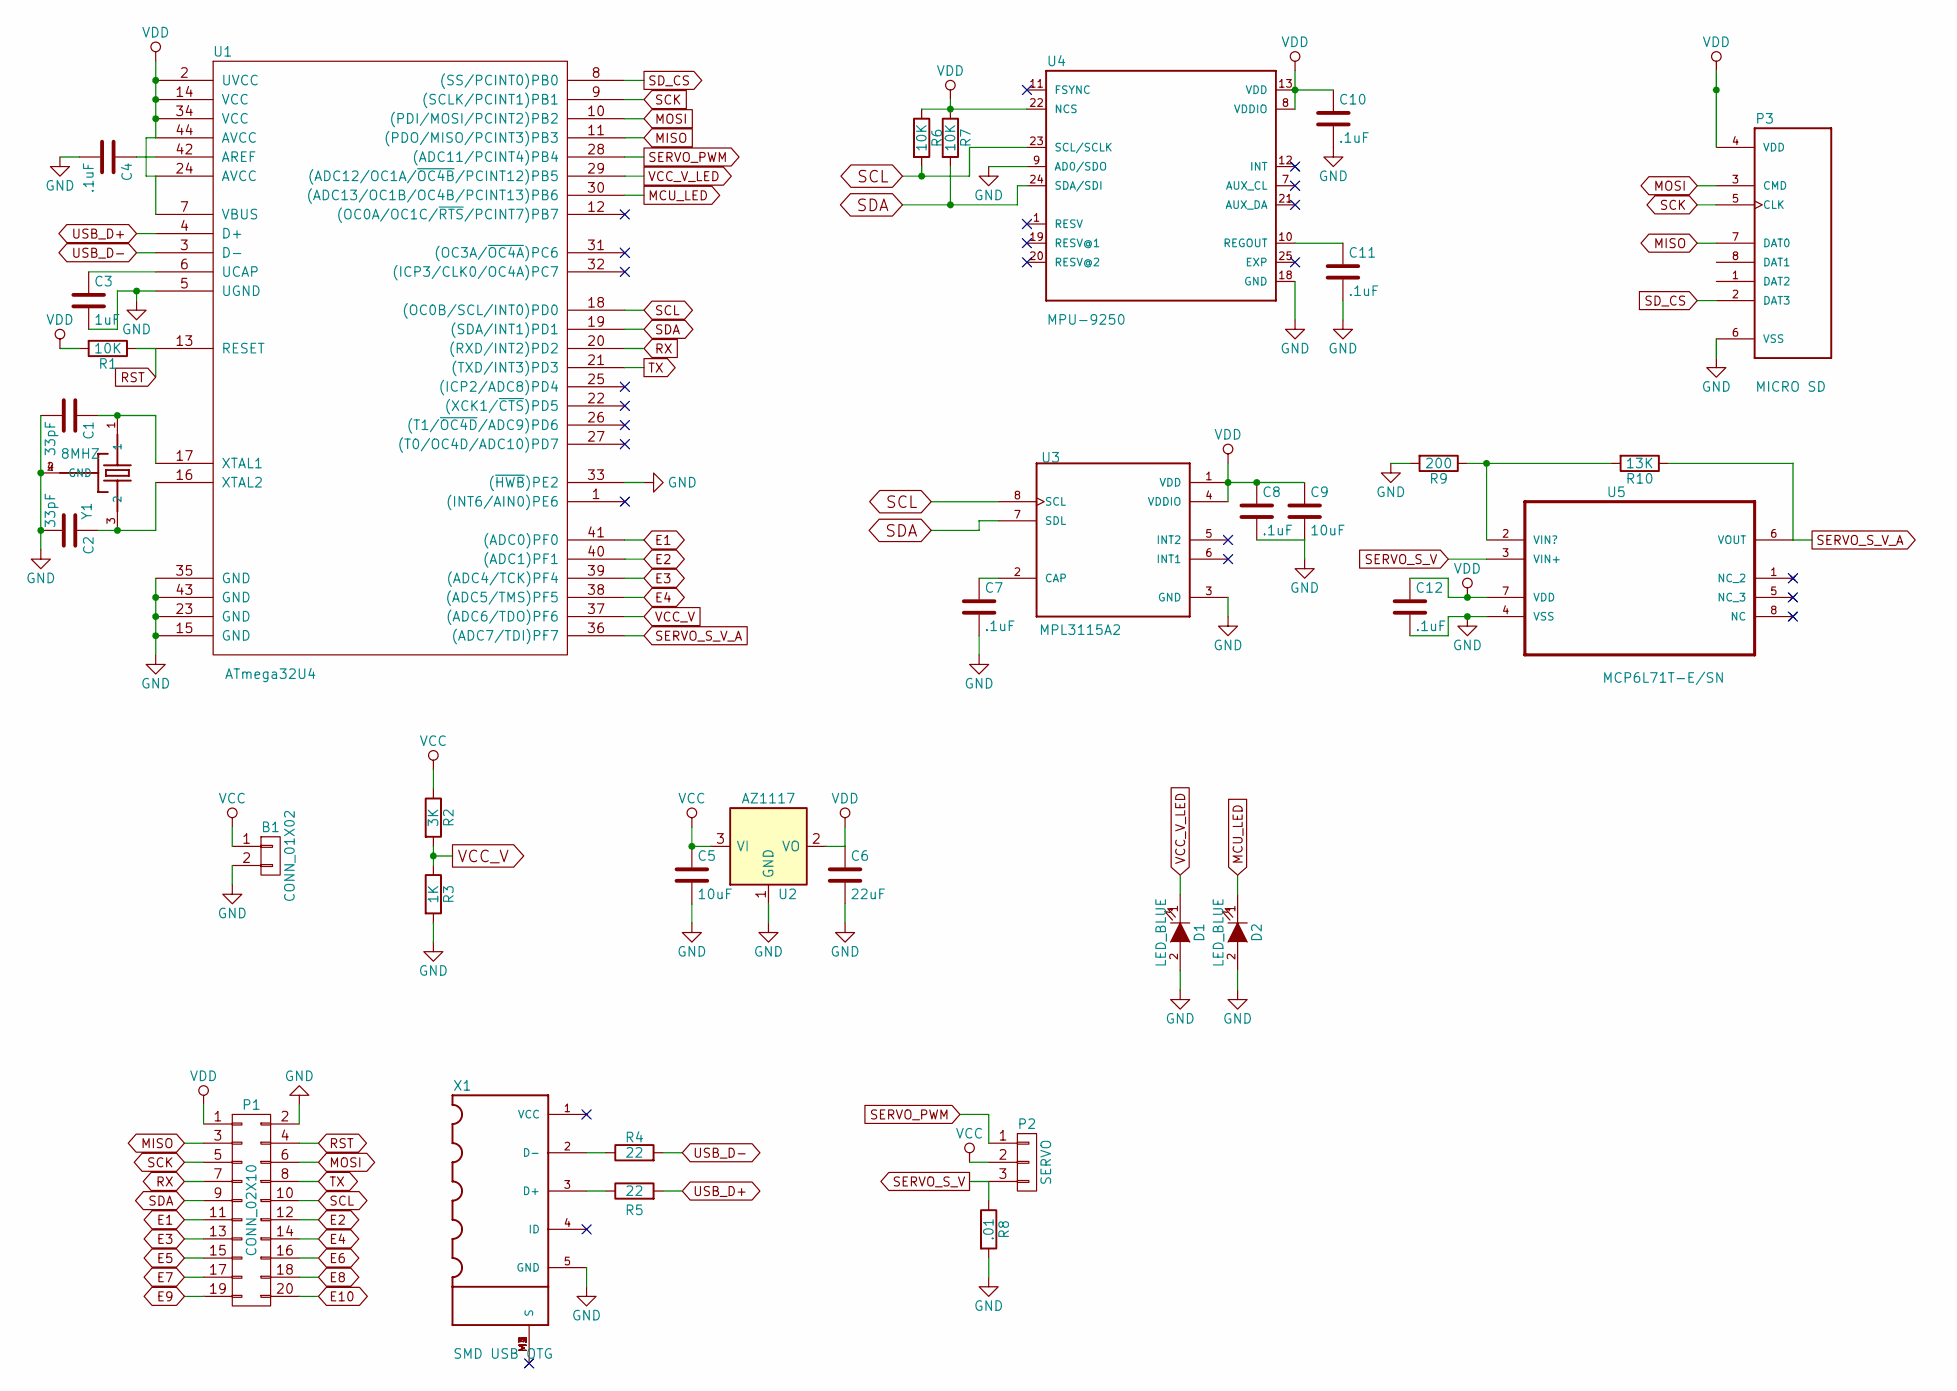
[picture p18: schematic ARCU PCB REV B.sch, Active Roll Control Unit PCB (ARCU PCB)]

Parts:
B1: CONN_01X02; XT60
C1, C2: 33pF; C_0805
C3: 1uF; C_0805
C4, C7, C8, C10, C11, C12: .1uF; C_0805
C5, C9: 10uF; C_0805
C6: 22uF; C_0805
D1, D2: LED_BLUE; LED_0805
P1: CONN_02X10; Card Edge 2x10 B
P2: SERVO; Pin_Header_Straight_1x03
P3: MICRO SD; HRS_DM3CS-SF
R1, R6, R7: 10K; R_0805
R2: 3K; R_0805
R3: 1K; R_0805
R4, R5: 22; R_0805
R8: .01; R_0805
R9: 200; R_0805
R10: 13K; R_0805
U1: ATmega32U4; TQFP-44_10x10mm_Pitch0.8mm
U2: AZ1117; SOT-223
U3: MPL3115A2; PSON125P300X500X120-8N
U4: MPU-9250; QFN40P300X300X105-25N
U5: MCP6L71T-E/SN; SOIC127P600X175-8N
X1: SMD USB OTG; UX60-MB-5ST
Y1: 8MHZ; OSCSC500X320X110-4N

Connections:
E1: P1.11, U1.41 ((ADC0)PF0)
E2: P1.12, U1.40 ((ADC1)PF1)
E3: P1.13, U1.39 ((ADC4/TCK)PF4)
E4: P1.14, U1.38 ((ADC5/TMS)PF5)
E5: P1.15
E6: P1.16
E7: P1.17
E8: P1.18
E9: P1.19
E10: P1.20
GND: B1.2, C1.2, C2.2, C3.2, C4.2, C5.2, C6.2, C7.2, C8.2, C9.2, C10.2, C11.2, C12.2, D1.2 (A), D2.2 (A), P1.2, P3.6 (VSS), R3.2, R8.2, R9.2, U1.5 (UGND), U1.15 (GND), U1.23 (GND), U1.33 ((~HWB~)PE2), U1.35 (GND), U1.43 (GND), U2.1 (GND), U3.3 (GND), U4.9 (AD0/SDO), U4.18 (GND), U5.4 (VSS), X1.5 (GND), Y1.2 (GND), Y1.4 (GND)
MCU_LED: D2.1 (K), U1.30 ((ADC13/OC1B/OC4B/PCINT13)PB6)
MISO: P1.3, P3.7 (DAT0), U1.11 ((PDO/MISO/PCINT3)PB3)
MOSI: P1.6, P3.3 (CMD), U1.10 ((PDI/MOSI/PCINT2)PB2)
unnamed: C1.1, U1.17 (XTAL1), Y1.1
unnamed: C2.1, U1.16 (XTAL2), Y1.3 (2)
unnamed: C3.1, U1.6 (UCAP)
unnamed: C4.1, U1.42 (AREF)
unnamed: C7.1, U3.2 (CAP)
unnamed: C11.1, U4.10 (REGOUT)
unnamed: R4.1, X1.2 (D-)
unnamed: R5.1, X1.3 (D+)
unnamed: R9.1, R10.2, U5.2 (VIN?)
unnamed: X1.M1 (S), X1.M2 (S), X1.M3 (S), X1.M4 (S)
RST: P1.4, R1.1, U1.13 (RESET)
RX: P1.7, U1.20 ((RXD/INT2)PD2)
SCK: P1.5, P3.5 (CLK), U1.9 ((SCLK/PCINT1)PB1)
SCL: P1.10, R6.2, U1.18 ((OC0B/SCL/INT0)PD0), U3.8 (SCL), U4.23 (SCL/SCLK)
SDA: P1.9, R7.2, U1.19 ((SDA/INT1)PD1), U3.7 (SDL), U4.24 (SDA/SDI)
SD_CS: P3.2 (DAT3), U1.8 ((SS/PCINT0)PB0)
SERVO_PWM: P2.1, U1.28 ((ADC11/PCINT4)PB4)
SERVO_S_V: P2.3, R8.1, U5.3 (VIN+)
SERVO_S_V_A: R10.1, U1.36 ((ADC7/TDI)PF7), U5.6 (VOUT)
TX: P1.8, U1.21 ((TXD/INT3)PD3)
USB_D+: R5.2, U1.4 (D+)
USB_D-: R4.2, U1.3 (D-)
VCC: B1.1, C5.1, P2.2, R2.1, U2.3 (VI)
VCC_V: R2.2, R3.1, U1.37 ((ADC6/TDO)PF6)
VCC_V_LED: D1.1 (K), U1.29 ((ADC12/OC1A/~OC4B~/PCINT12)PB5)
VDD: C6.1, C8.1, C9.1, C10.1, C12.1, P1.1, P3.4 (VDD), R1.2, R6.1, R7.1, U1.2 (UVCC), U1.7 (VBUS), U1.14 (VCC), U1.24 (AVCC), U1.34 (VCC), U1.44 (AVCC), U2.2 (VO), U3.1 (VDD), U3.4 (VDDIO), U4.8 (VDDIO), U4.13 (VDD), U4.22 (NCS), U5.7 (VDD)

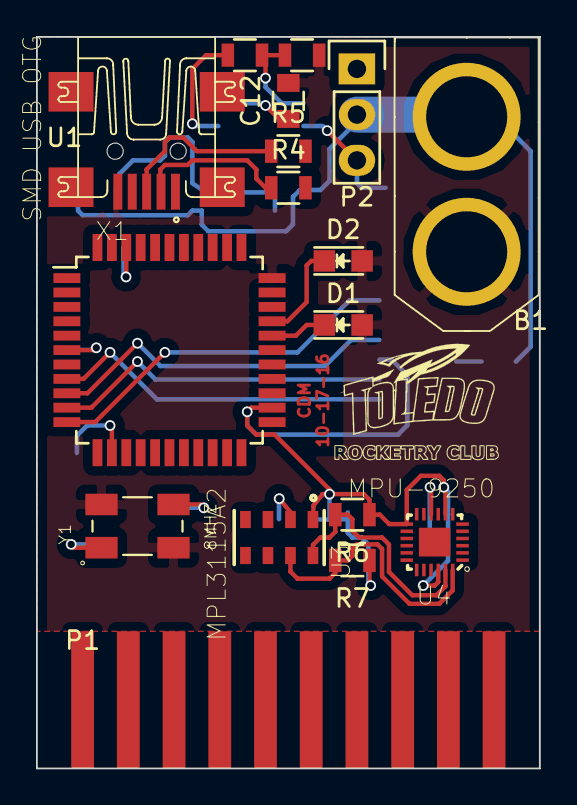
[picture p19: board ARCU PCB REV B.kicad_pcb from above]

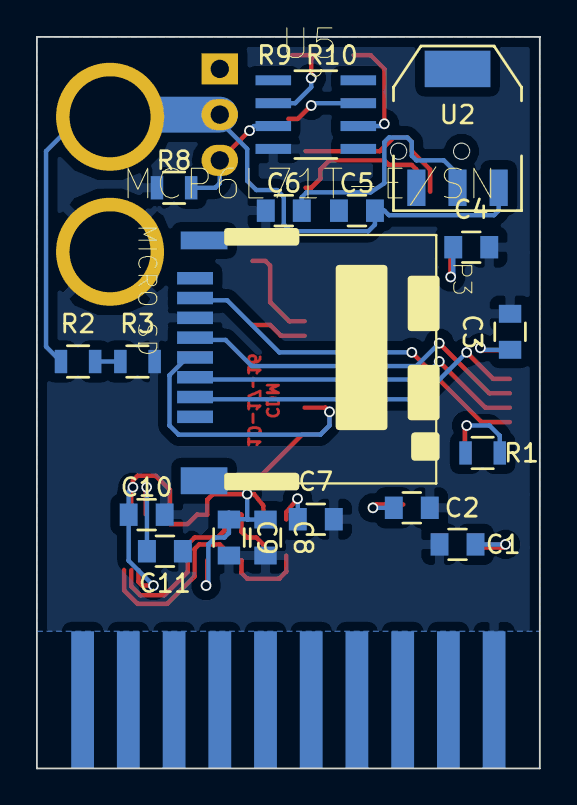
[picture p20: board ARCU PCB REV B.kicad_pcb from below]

Board: 2 copper layers, 27.9 x 40.6 mm, 35 parts (18 on the bottom side), 34 nets.

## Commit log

2016-11-09 added BOM
    [ARCU PCB REV A BOM.ods]
2016-11-15 Add files via upload
    Added gerber files
    [ARCU REV A RELEASE-B.Cu.gbl, ARCU REV A RELEASE-B.Mask.gbs, ARCU REV A RELEASE-B.SilkS.gbo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]
2016-12-31 Added REV B
    [ARCU REV B RELEASE.kicad_pcb, ARCU REV B RELEASE.sch]
2017-02-28 Split RELEASE into sub folders. Added MOD footprints
    [ARCU BREAKOUT REV A RELEASE.kicad_pcb, ARCU BREAKOUT REV A RELEASE.sch, ARCU ESP8266 REV A RELEASE.kicad_pcb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]
2018-01-01 new folders
    [ARCU BREAKOUT REV A RELEASE.kicad_pcb, ARCU BREAKOUT REV A RELEASE.sch, ARCU ESP8266 REV A RELEASE.kicad_pcb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]
